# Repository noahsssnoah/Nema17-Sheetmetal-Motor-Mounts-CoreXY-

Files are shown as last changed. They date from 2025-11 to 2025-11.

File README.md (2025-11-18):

*Exclaimer: Designed for 4040 Profiles, may work with 4020 profiles.*

# Nema17-Sheetmetal-Motor-Mounts-CoreXY-
I developed a high-performance sheet-metal motor mount specifically for NEMA17 stepper motors in CoreXY 3D printers. The design delivers maximum rigidity to minimize deformation and significantly improves precision compared to typical 3D-printed mounts. Its aluminum surface enhances thermal performance by enabling effective heat dissipation and acting as a thermal buffer. The mount is engineered as a compact assembly for straightforward, cost-efficient manufacturing, combining precision, durability, and practicality.

Objectives for development of this sheetmetal part are:
- increased version compatibility [V-Slot-Wheels-Version; MGN9H-Rail-Version; MGN12H-Rail-Version]
- designed for Nema17x60mm works also with shorter models of Nema17 Steppers
- cost-efficient manufacturing
  - sheetmetal design
    - excellent material utilization
  - no CNC operated systems needed (but possible via third-party-manufacturers)
- optimized thermal specs
  - 200x better thermal conductivity
    - motor heat gets dissipated through sheetmetal mount
    - motormount offers more surface to dissipate heat through convection and radiation
  - lower heat capacity
- increased rigidty
  - 20x better rigitdy/Youngs Modulus
  - deviation in the hundredths to tenth mm range
- designed to work with idlers instead of flange bearing to prevent belts from slipping/drifting
- lighter motor mount design lowers the center of mass, which positivly influences [Input-Shaping](https://github.com/Frix-x/klippain-shaketune) results

# CAD
CAD-Files are available [here](./CAD).

# Drawing and Template
Drawing-Files are available [here](./drawings).

*Note:* Drawing only includes A-Stepper Mount, as both mounts are symmetrical. Manufacture for A or B Stepper is determined by direction/side of bending.

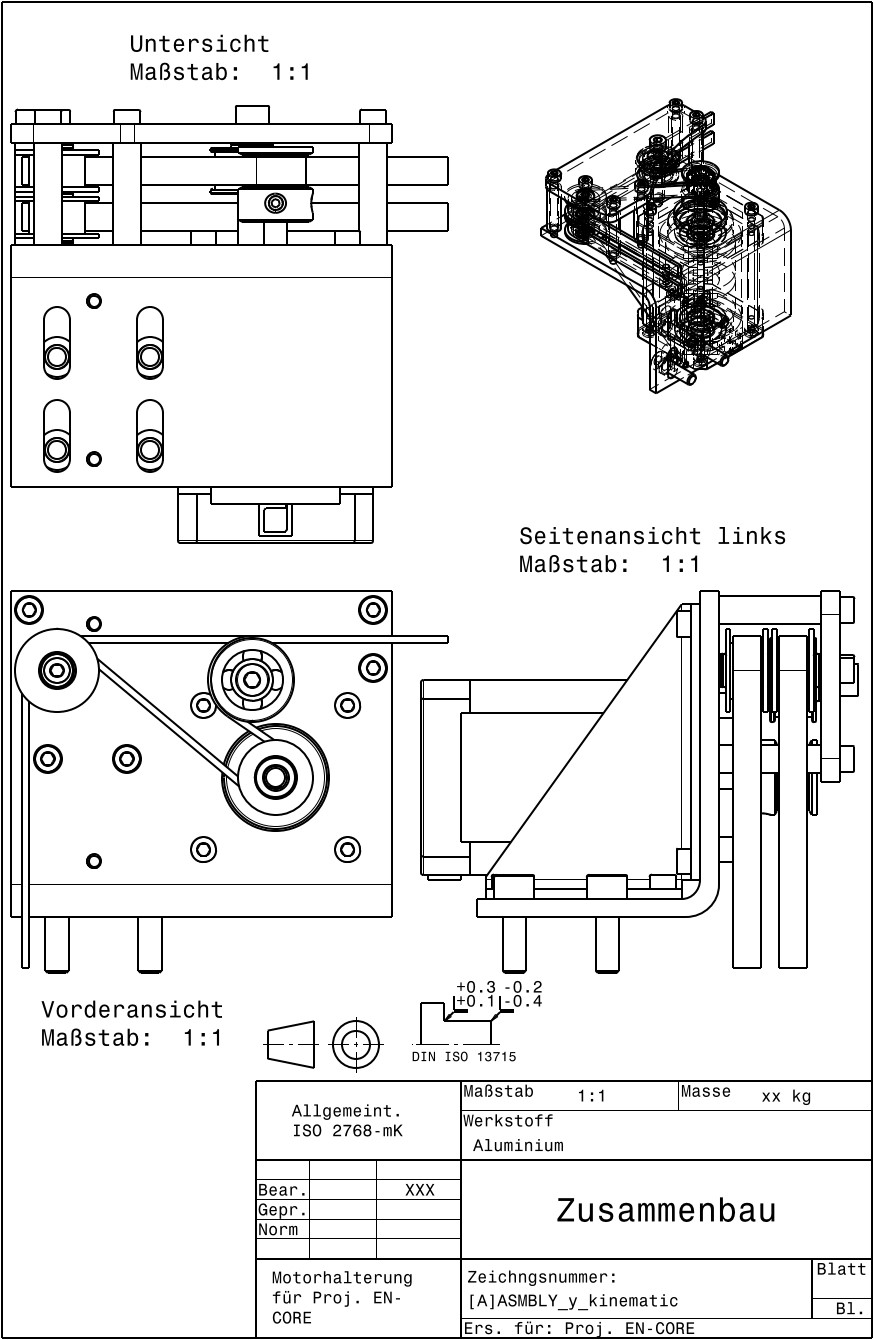
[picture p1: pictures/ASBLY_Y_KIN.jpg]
ASBLY_Y_KIN


# Genereal Bill of Materials (BOM)
Tools:
- M3/M4 Drill
- M3/M4 Threading Tool
- Press Brake/Bending Machine
- saw

Assembly Parts:
- Nema17 Stepper motor
- GT2 20T Pulley
- 2x GT2 20T Idler (no teeth)
- MF 84 ZZ Flange Bearing (comes with Ender 3 V2; *Ender 3 may be diffrent!*)
- Spacer Sleeves
  - 5x 6x4x22 (inner- x outer- x length) -diameter
  - 1x 6x4x11 (inner- x outer- x length) -diameter
- Cylinder head screws
  - 4x M3x6
  - 4x M5x16
  - 6x M3x30
  - 4x M3x8
  - 1x M4x30
  - 8x M3 Washer
  - 2x M4 Washer (i ditched the 6x4x11 spacer sleeve and used instead many M4 Wahshers see [Reference Pictures]
- 4mm aluminium sheetmetal (main-/top-body) see [here](./CAD) or [here](./drawings).
- 1.5mm aluminium sheetmetal see also [here](./CAD) or [here](./drawings).

# Manufacturing-tips
- holes in top-plate can/should be al little bigger than the ones from the main-body so screws don't get misaligned during assembly
  - also neutralisies sheer force on screws
**Parts and Drawing going to be updated by me soon**

# Deviation Profile
Deviation profile shows stress distribution from sheer forces over the spacer sleeves as well as where deformations is happening. Deviation is scaled to factor 100 to actually see deformation.

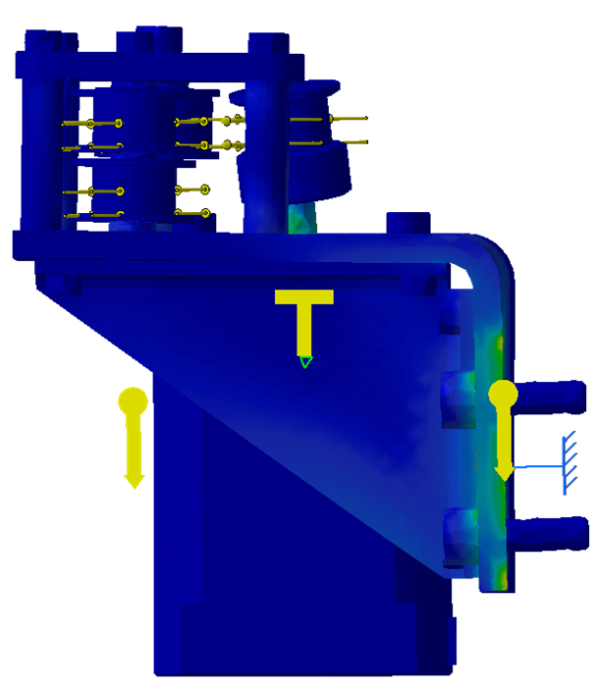
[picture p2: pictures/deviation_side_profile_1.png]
deviation_side_profile_1

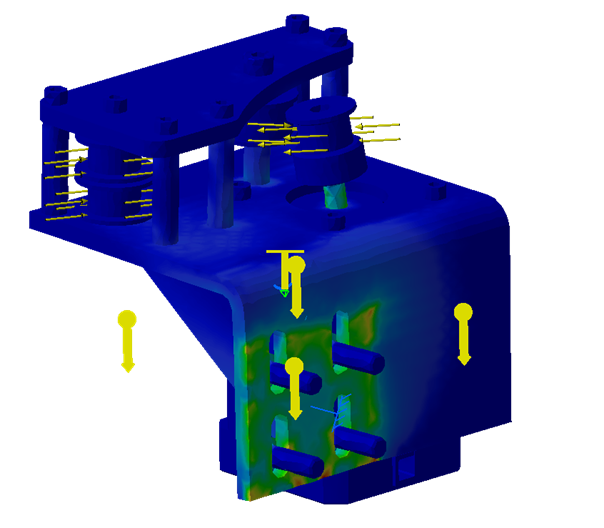
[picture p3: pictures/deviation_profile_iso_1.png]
deviation_profile_iso_1

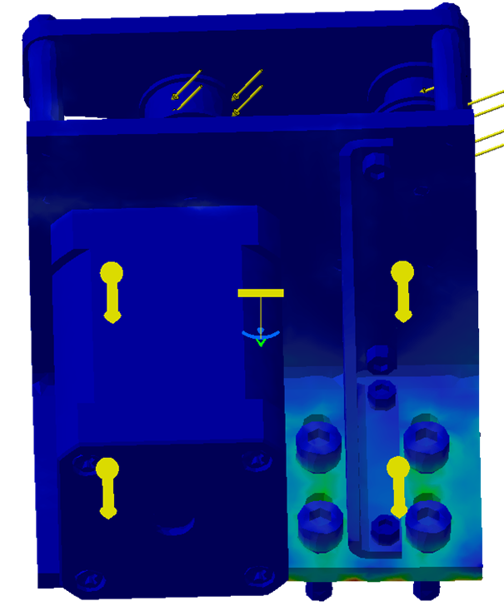
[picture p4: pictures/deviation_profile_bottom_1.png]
deviation_profile_bottom_1


# Reference Pictures

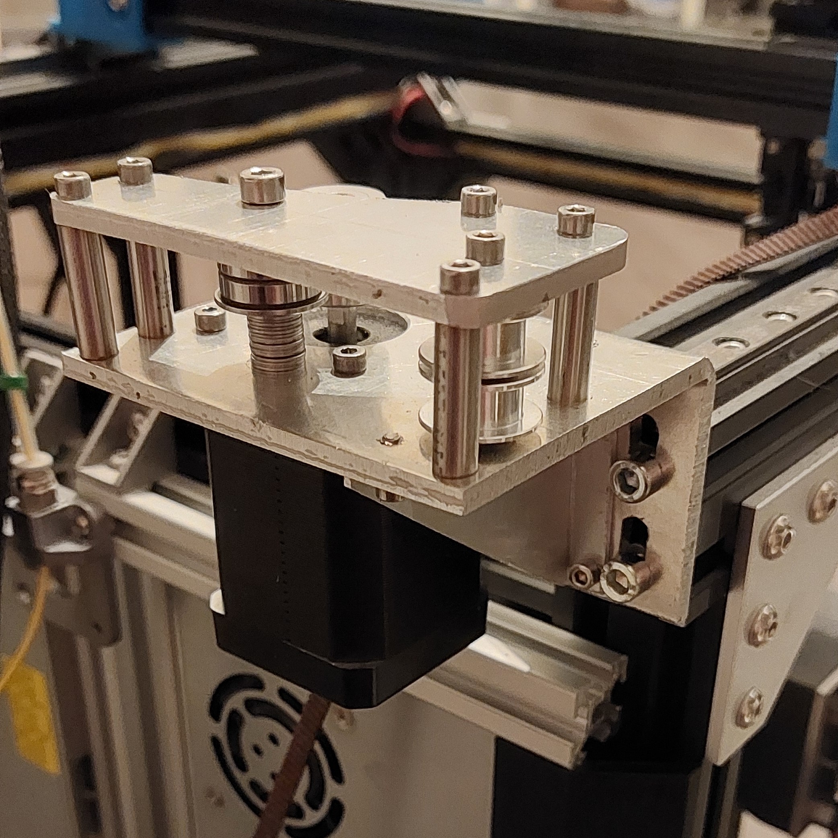
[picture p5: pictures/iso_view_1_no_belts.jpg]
iso_view_1_no_belts

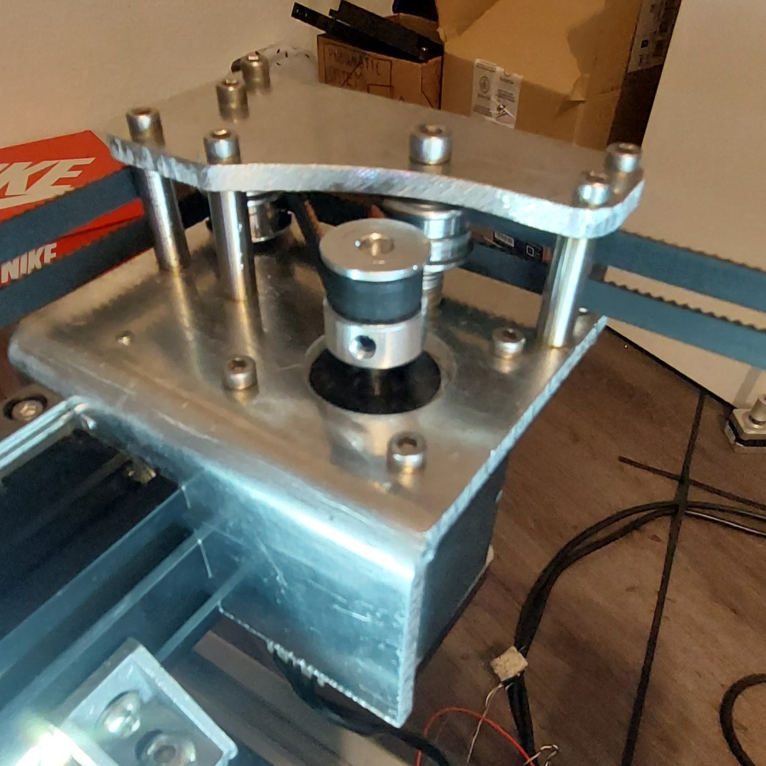
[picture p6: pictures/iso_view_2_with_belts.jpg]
iso_view_2_with_belts

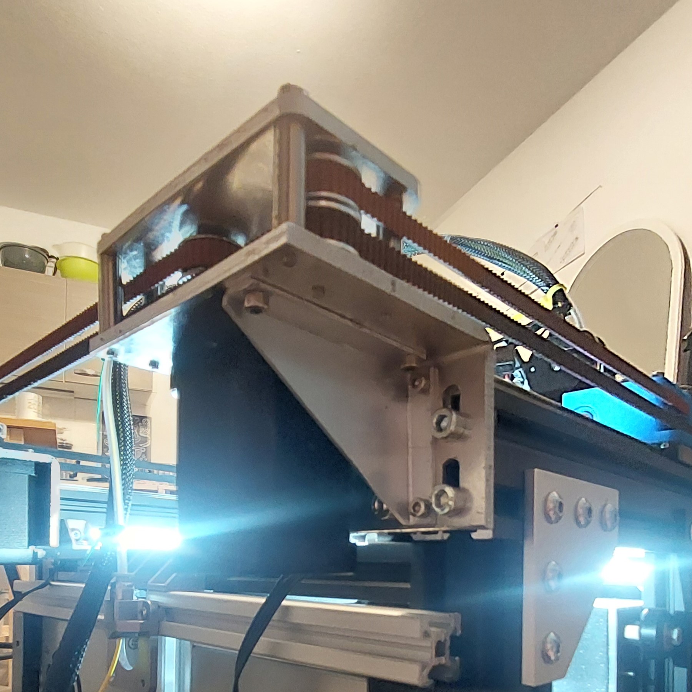
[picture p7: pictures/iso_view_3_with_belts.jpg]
iso_view_3_with_belts


#
**This project is a user modification for DuEnder by Sergei Irbis.**

DuEnder Discord: (https://discord.com/invite/ae44FHv786)

Sergei's YT-Channel: (https://www.youtube.com/@Irbis3D)

#

<a href="https://github.com/noahsssnoah/Nema17-Sheetmetal-Motor-Mounts-CoreXY-"> Nema17-Sheetmetal-Motor-Mounts-CoreXY-</a> © 2025 by <a href="https://github.com/noahsssnoah">noahsssnoah</a> is licensed under <a href="https://creativecommons.org/licenses/by-nc-sa/4.0/">CC BY-NC-SA 4.0</a>

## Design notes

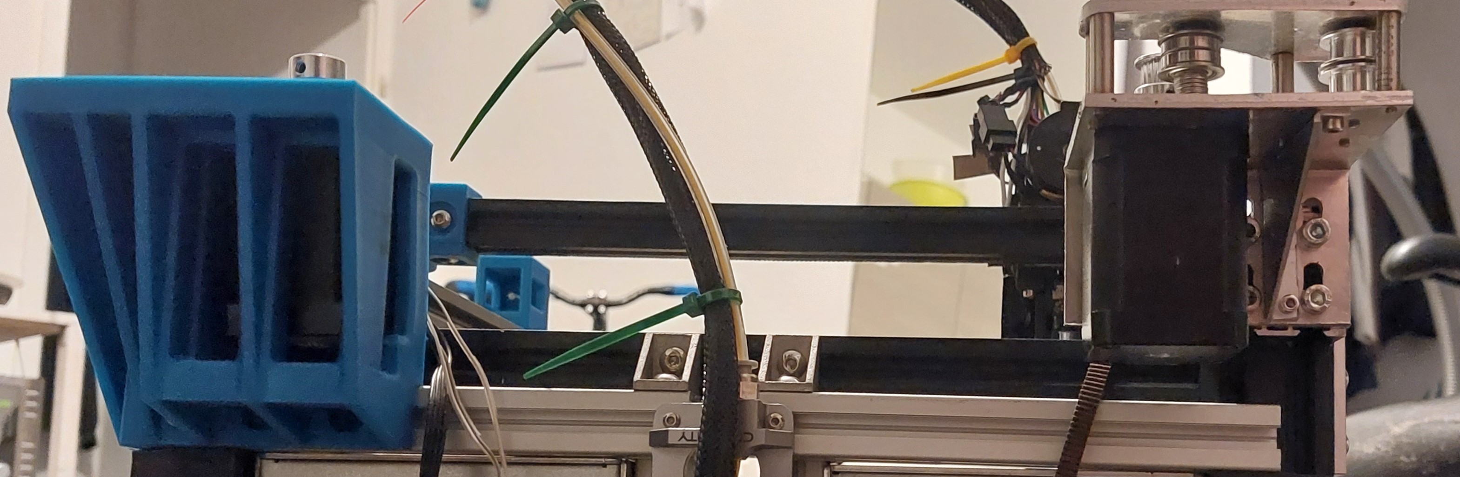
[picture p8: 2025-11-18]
pictures/comparison_1_rear_view.jpg

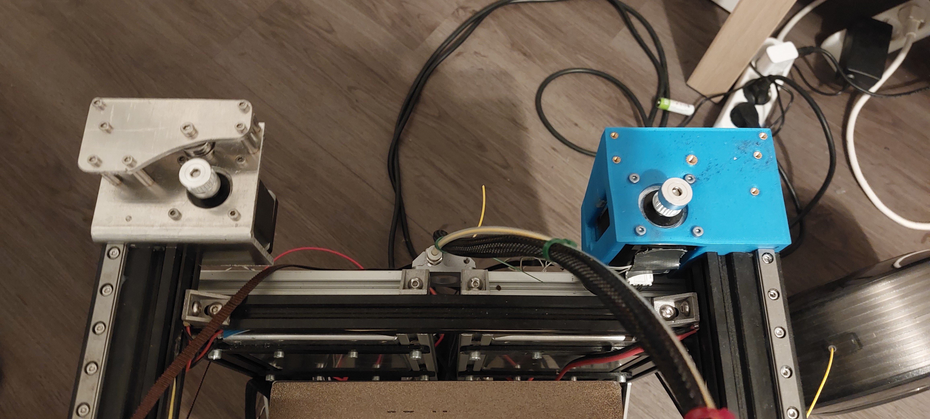
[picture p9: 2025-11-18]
pictures/comparison_1_top_view.jpg

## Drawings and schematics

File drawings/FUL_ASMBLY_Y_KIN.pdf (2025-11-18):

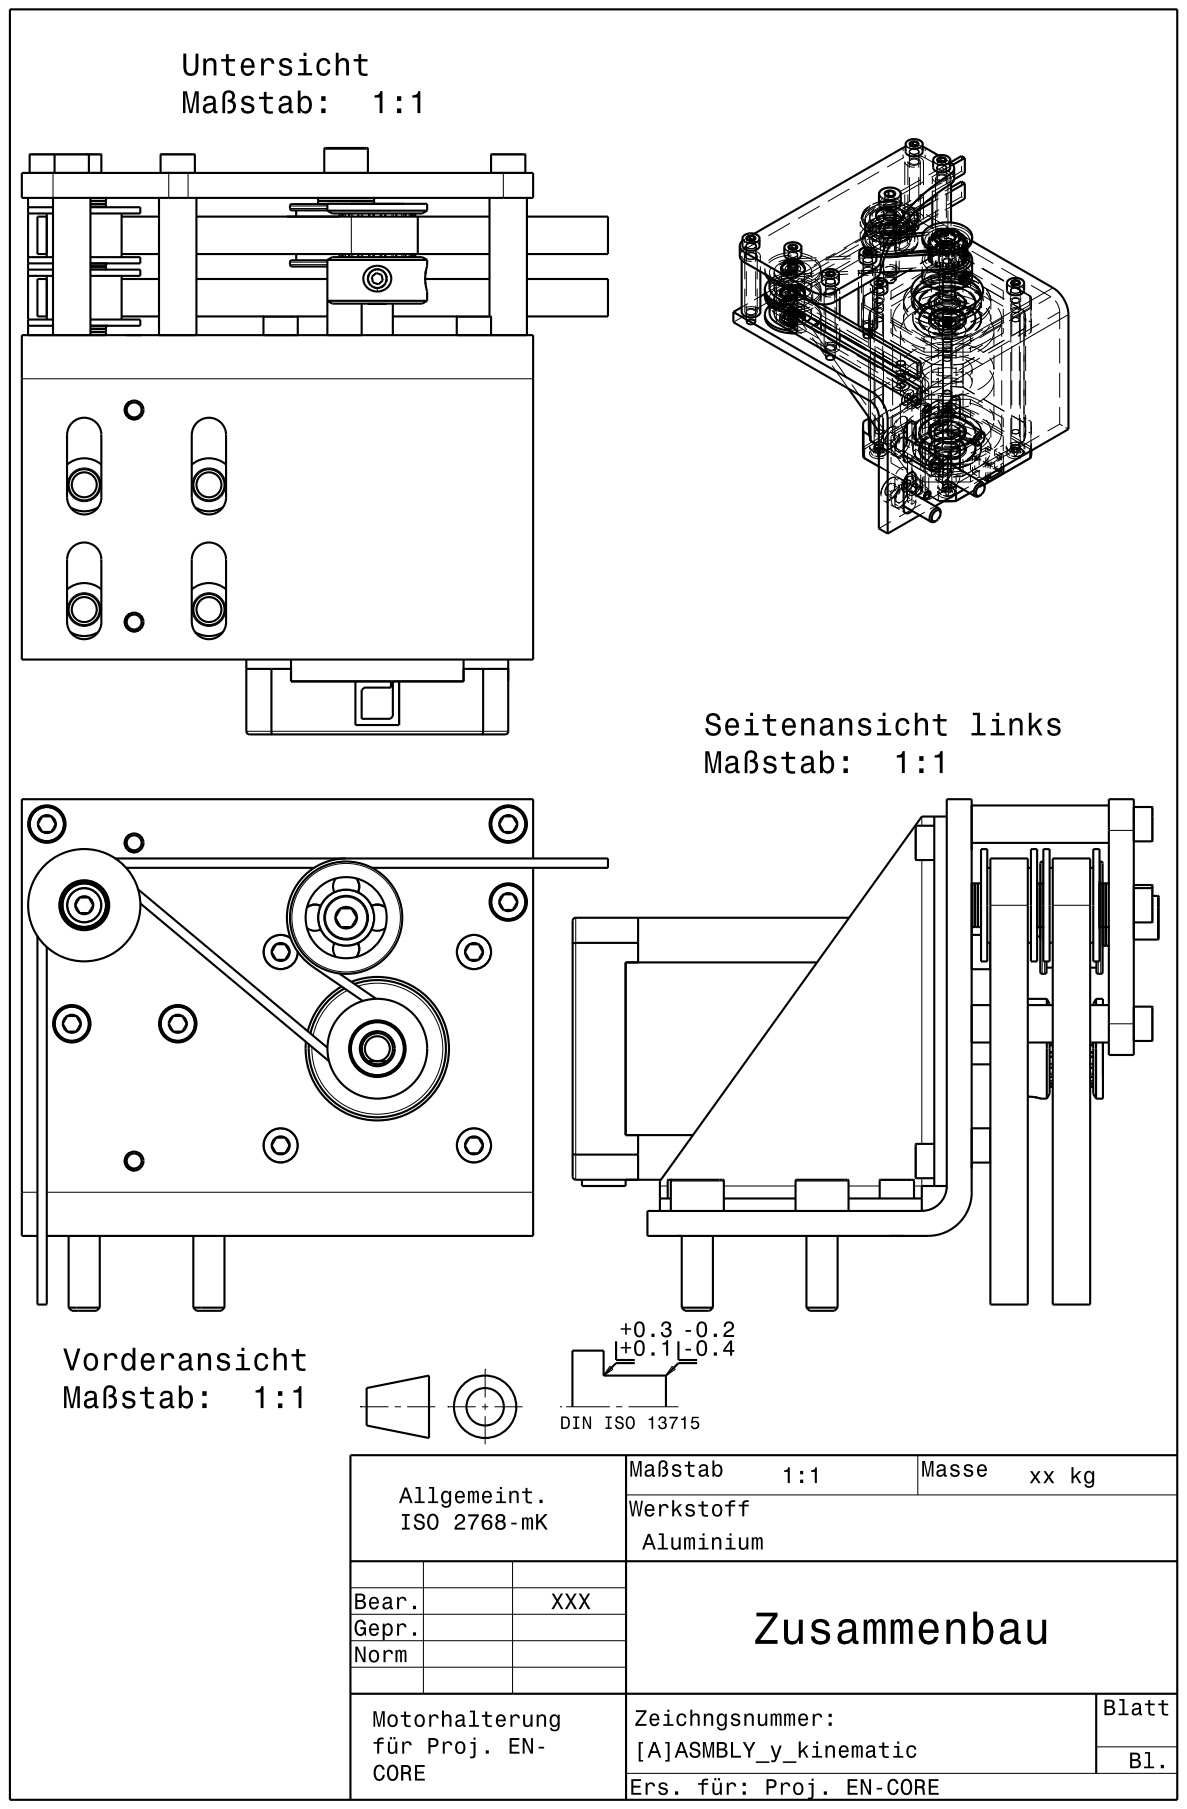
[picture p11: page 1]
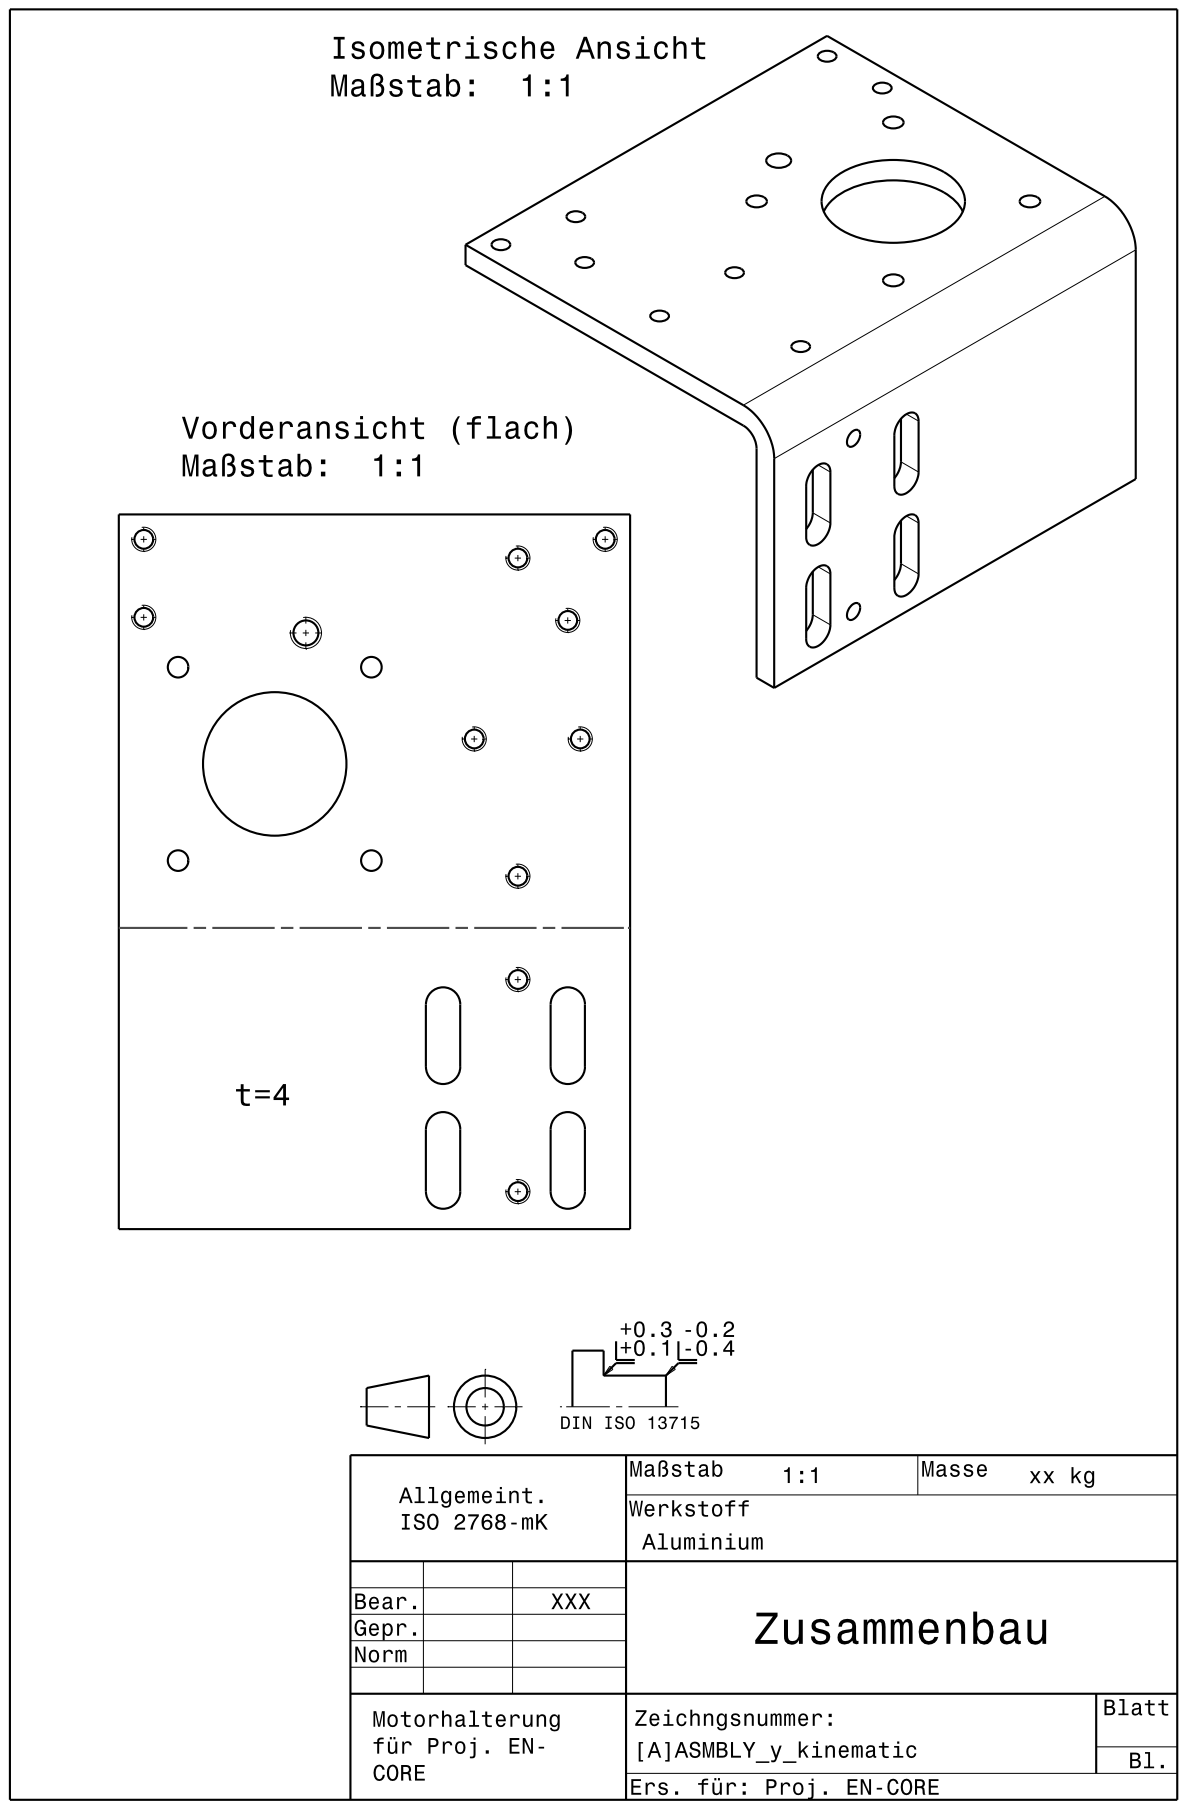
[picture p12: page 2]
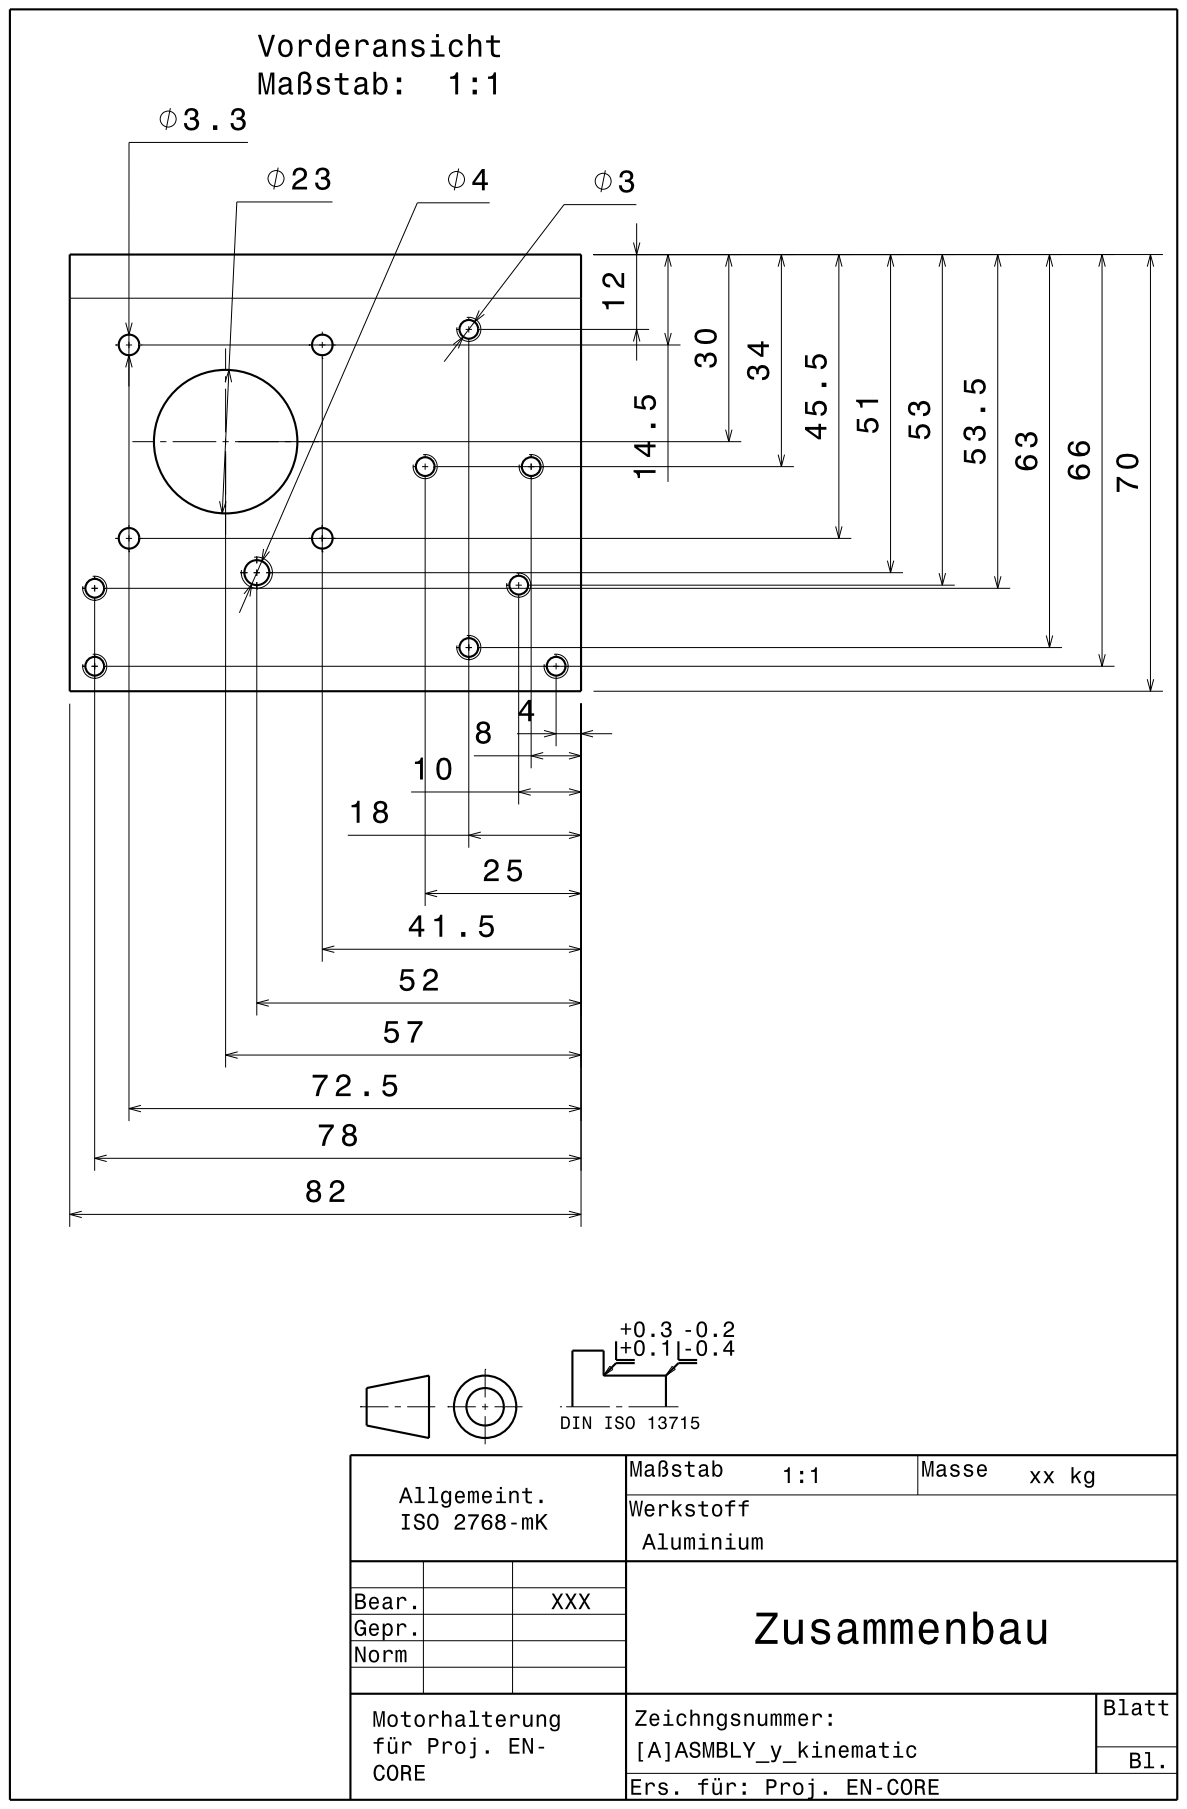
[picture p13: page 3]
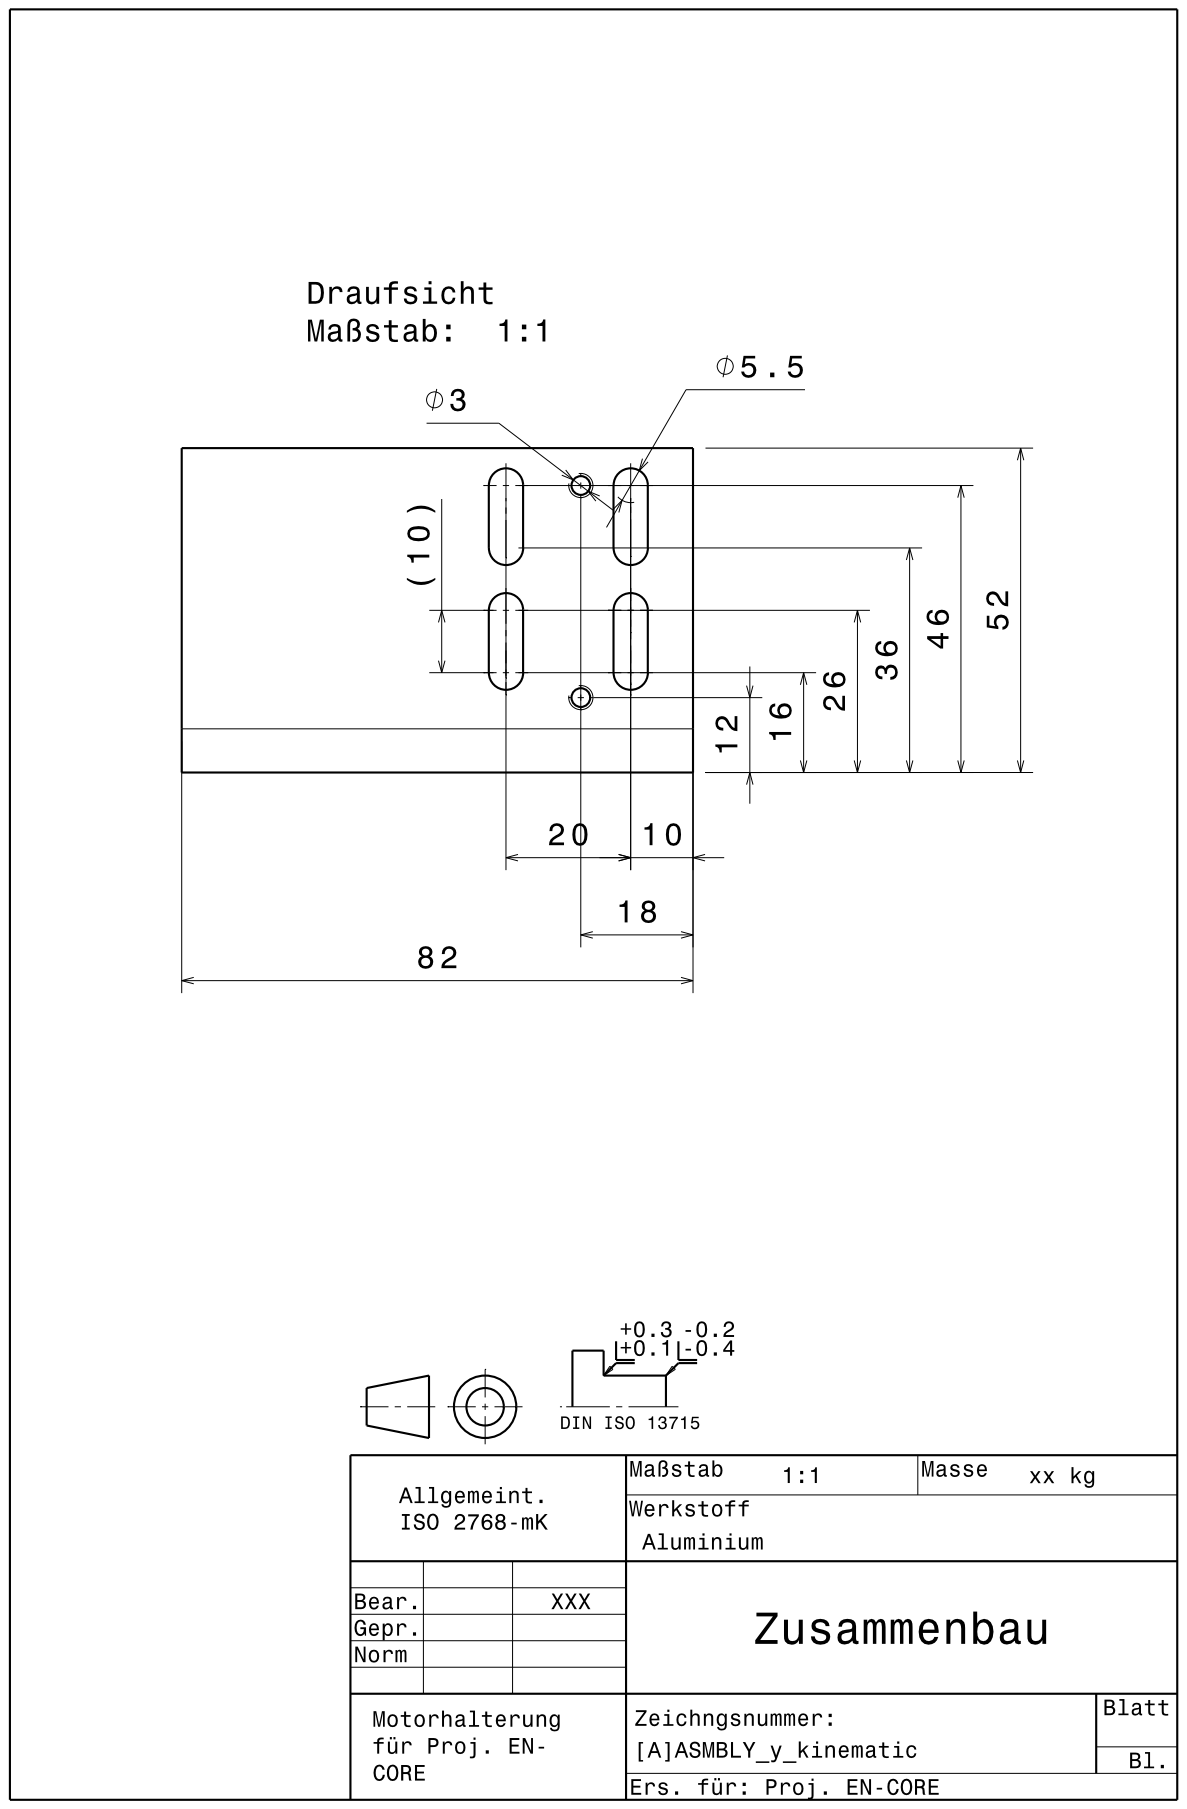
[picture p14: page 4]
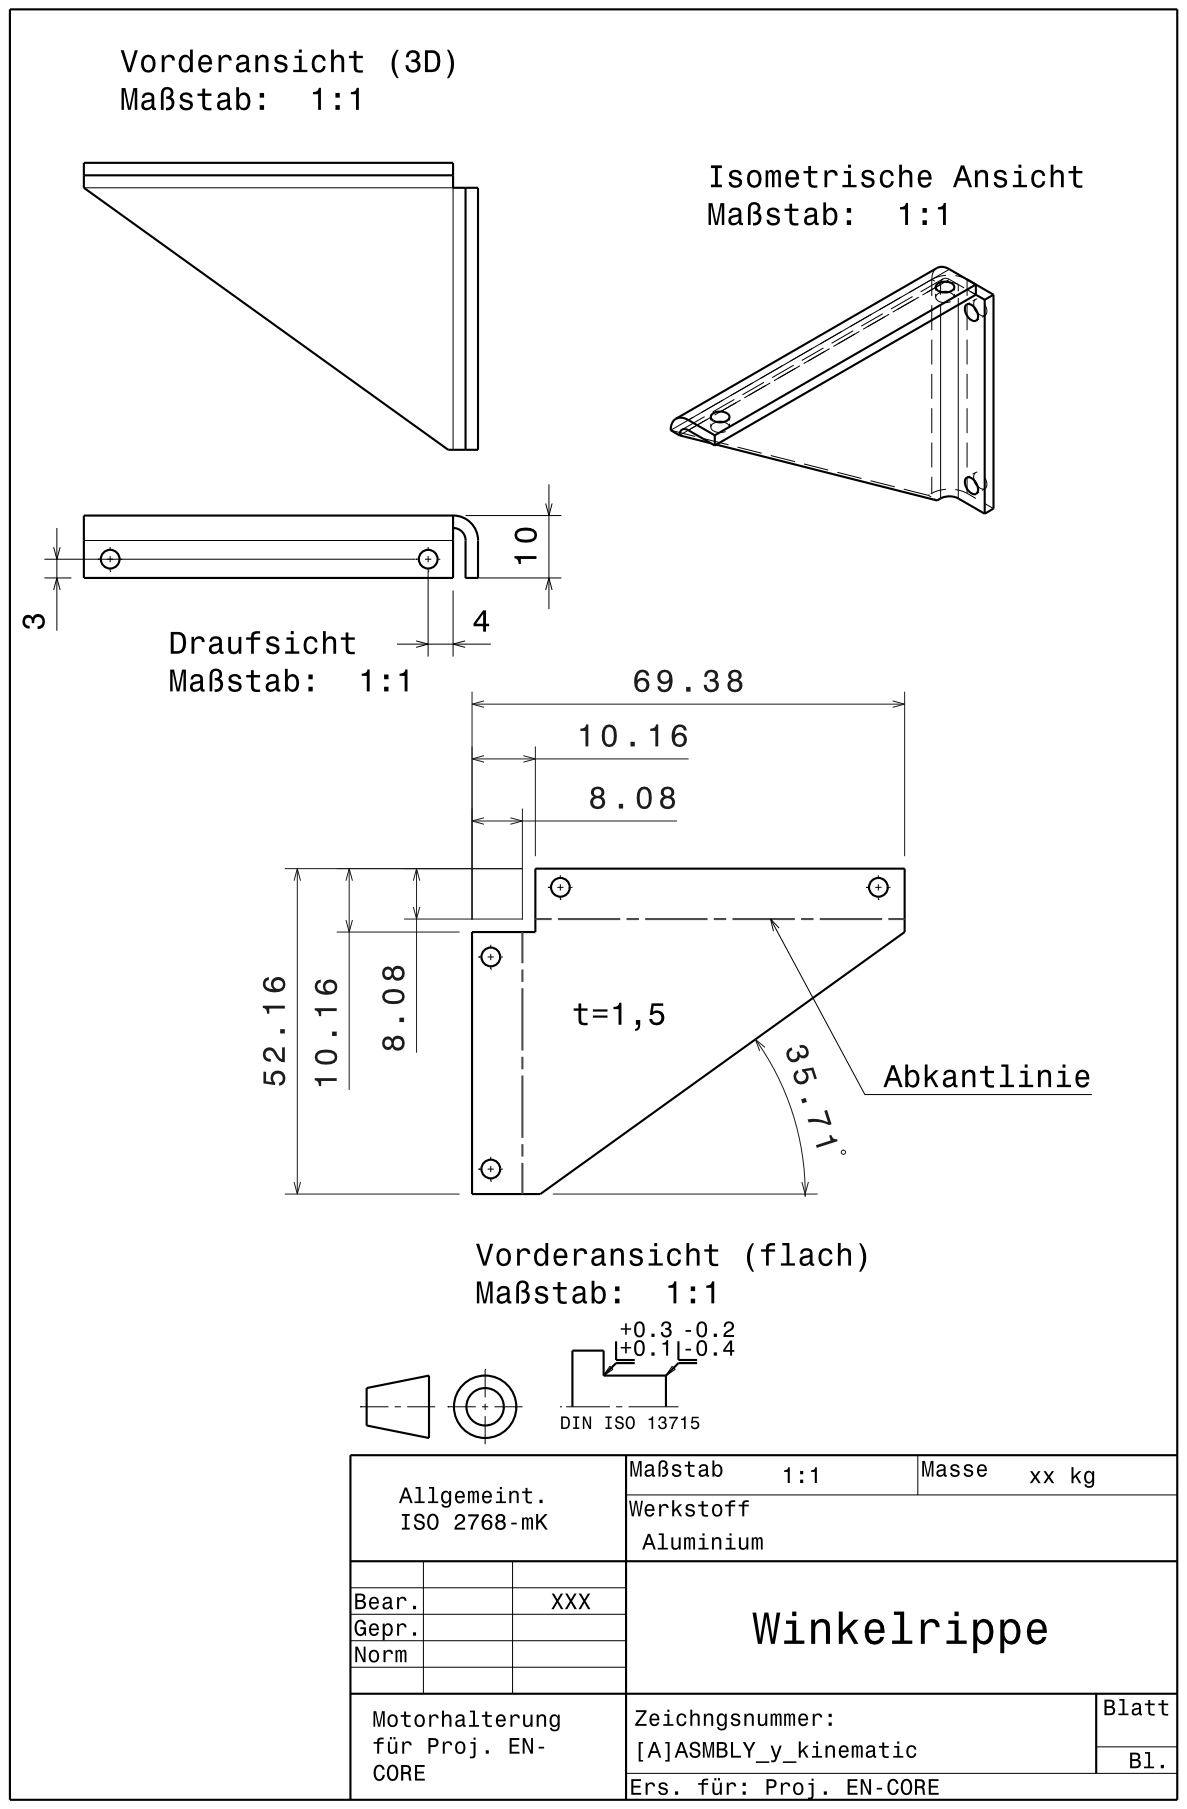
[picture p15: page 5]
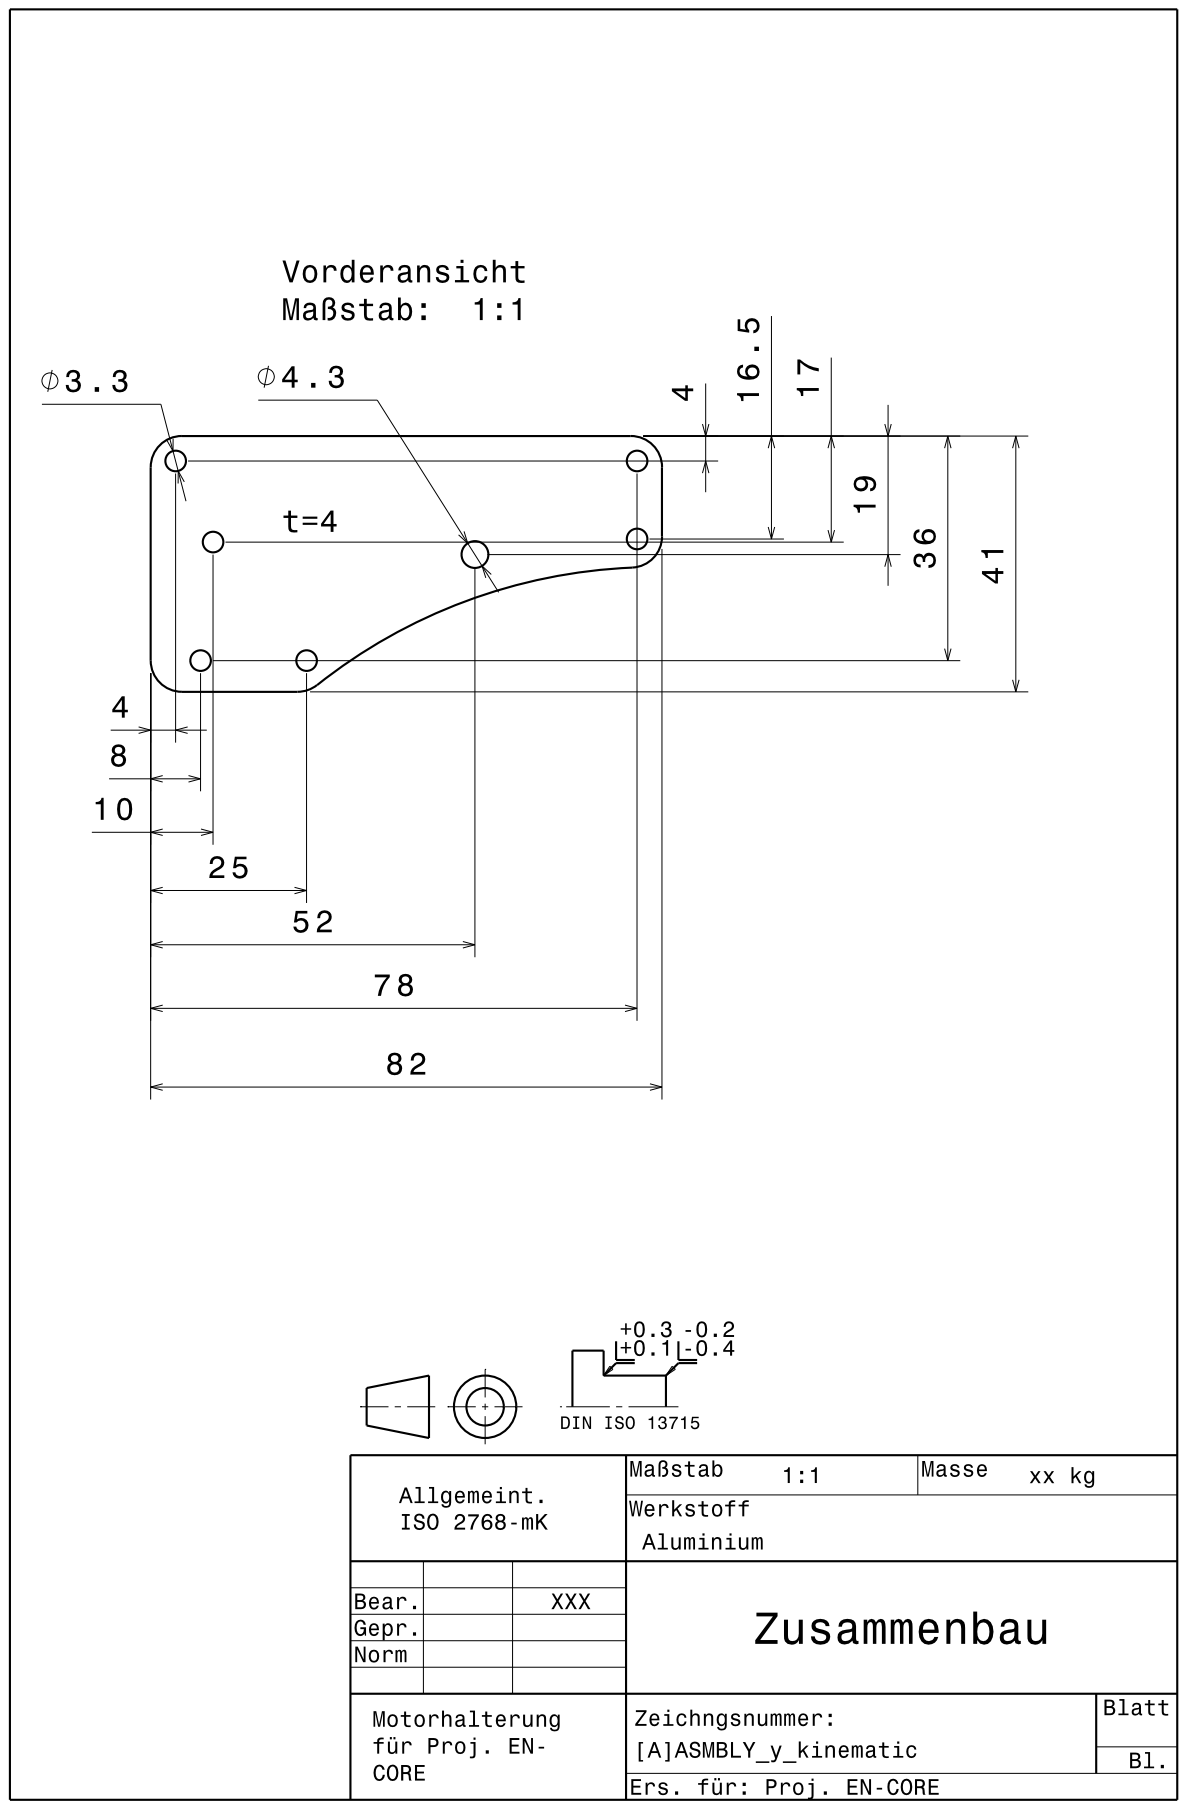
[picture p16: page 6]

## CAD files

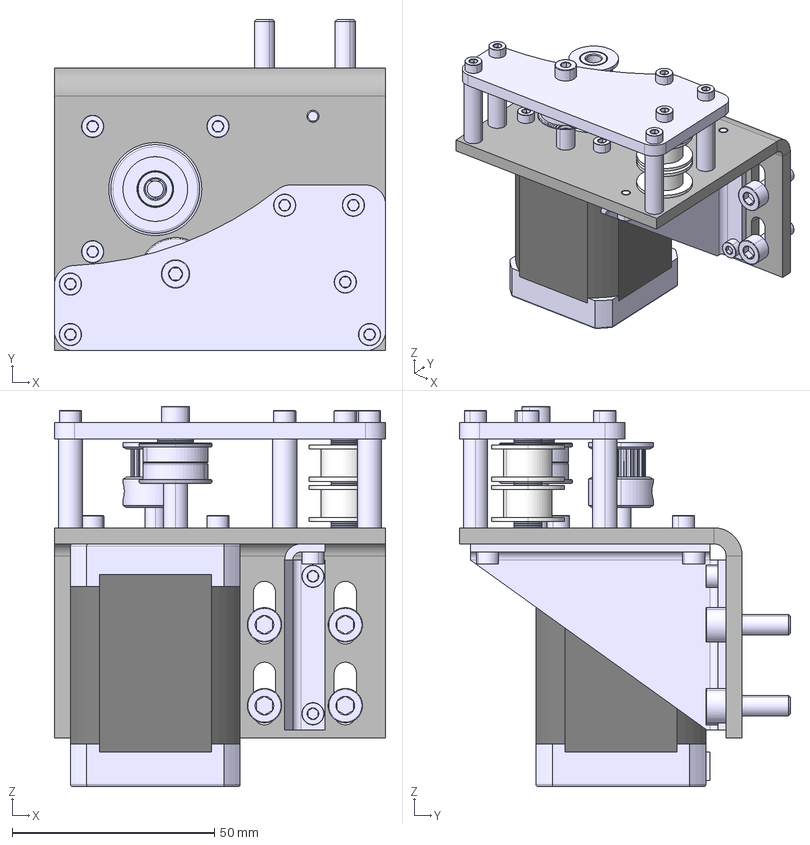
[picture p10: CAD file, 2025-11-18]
CAD/[A]ASMBLY_y_kinematic.stp
82.0 x 82.0 x 94.0 mm
NEMA17_60
MF84ZZ x 2
[A]Blech_Motorhalterung
GT2_20T
POWGE 2GT idler 20T B3 x 2
[A]Blech_Motorhalterung_Winkelrippe
[A]Blech_Motorhalterung_Top
y_distanzhuelse x 5
y_distanzhuelse.2
Zylinderschraube ISO 4762 - M3x6 x 4
Zylinderschraube ISO 4762 - M5x16 x 4
Zylinderschraube ISO 4762 - M3x30 x 6
Zylinderschraube ISO 4762 - M3x8.1 x 4
Zylinderschraube ISO 4762 - M4x30
M3_Unterlegscheibe x 8
M4_Unterlegscheibe x 2
